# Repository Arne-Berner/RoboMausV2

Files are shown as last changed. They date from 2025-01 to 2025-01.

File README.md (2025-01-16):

# Goal
- build a micromouse (from here on out called "rat") from scratch

# Motivation
## The fear of the unknown
I have been working with electronics for a while now, but I never really got into PCB design. I always thought it was too complicated and I would never be able to do it. But I also always wanted to build a micromouse. So I thought, why not combine the two and learn something new in the process.

That being said I also wanted to use my 3D printer more and get rid of that fear that accompanies anything new. Doing this project I feel like I will be able to create electronic devices much more easily in the future. Not only because I learned some tricks on my way, but because I simply have done it before.

## Beginner to Intermediate Rust Project
Let's be honest, coding for embedded systems sound hard. Rust also sounds hard. But weirdly enough, those two things combined are much easier than I thought! I want to provide all the code I used for this project for anyone interested. If you feel like creating electronic devices could be fun, give it a try! Especially the esp32 and rust go really well together. You can [try out Rust on the ESP32 on Wokwi](https://wokwi.com/).

# Parts with their Voltage and Reason I used them

## Placed
### ESP32-s3-mini: 3.3V 
The reason I chose the s3-mini was because it wasn't much more expensive and I was not sure how much processing power will be needed for the project. If I had more time I probably would have chosen an esp32 from the c series. You don't need to use an esp32 at all for a micromouse, but I will need to send the map created by my SLAM-algorithm to my computer via wifi. The STM32 is the MCU that is used for most micromouse.

### USB-C: 5V output
Micro USB tend to break of more easily from PCBs and USB-C has the possibility of using more Volt in later designs, without changing too much.

### AMS1117-3.3: LDO that converts to 3.3V
This seems to be a very common LDO and even though the esp32 is somewhat capable of handling higher voltage than described in the datasheet, I didn't want my project to go up in flames at a bad time.

### L293D (better known as an H-Bridge)
This will let me use my 3.3V from the esp and my 8V from the LiPos to drive my motors. It usually takes one source that ranges from 5V to 36V and another source that will only take 5V. I will see how it works in the project. I could've used an smt h-bridge to minimize the size on the pcb, but running the h-bridge in the wrong manner can destroy it. If that happens (and it will happen) I would like to be able to replace it fast.

### TCS34725 (Color sensor): 2.7V - 3.6V / nom: 3V
I will need to detect the colors of certain places in the labyrinth as an extra task. This seems to be a common and cheap color sensor. It also has a rust library. 

### GY-521 or MPU-6050 (gyroscope sensor): 2.375V - 3.46V
This will help me position orientate my rat. I'm not sure yet, how I will combine this with the input I get from the encoder and what will be used primarily if there is a difference between the two. The mpu-6050 seems to be cheaper but has better specs.

## Not Placed
### SK6812MINI-B-012 (NeoPixel): 5V
This could be used for debugging purposes (and it looks cool), but it needs 5V and that would've drained the LiPos faster than I wanted them to. There is a 3V alternative to the 5V neopixel, but I could not find it on lcsc.

### AMS1117-5.0: LDO that converts to 5V
This would have been necessary if I used the Neopixel above or if the ams1117-3.3 would not be able to handle the lipo voltage.

# Learnings
## How to read a Datasheet instead of "read the datasheet"
When you start in electronics you hear "read the datasheet" a lot. It sounds like bad advice at first, because you probably are asking experienced people about very specific device and datasheets can be hundreds of pages long. Where to start reading up on it? What if there is a feature that you didn't know the name of? Most people rather stop than to "read the datasheet" without knowing where to look for the most important info. 

Later on it feels like "read the datasheet" really was the solution to most problems. But only seemingly so. Experts don't read the full datasheet, even if it is only a few pages long. They won't look at all the data. But they know how to skim the datasheet for the most important info and see if anything is readworthy. But I am no expert and I still need to find answers to my questions. So how to read a datasheet?

There are some basic informations that you most likely want to take a look at:
- volt and ampere (often found as VCC or Vin/Vout info)
- the pinout
- provided example schematics
- (footprints)
With those infos you will have most infos so that your ICs don't burst into flames. It also has the benefit, that most often when looking for those informations you will find other important or odd info that will help you with your project. Be aware that datasheets sometimes contain the data for many variations of IC.

## Copilot and co.
Reading the datasheet might be hard if it is in chinese or if it is hundreds of pages long. Using any LLM to get the gist of it or some pointers where to look for can be very helpfull. But be warned: Especially in electronics halucinations seem to occur very often. They should only be used, if you check the data afterwards. The pinout is very often wrong, the current and voltage vary from the real parts and you can't use it for example schematics. But it will give you words to look for in the datasheet that might be important. 

"What should I be aware of with part XY" or "What could go wrong with wiring X to Y" are the most helpfull prompts.

## Kicad
### Schematics
I like to start with everything at once and see everything come together at the end. But who would have thought that this is neither good in programming, nor in electronics? 

The next project I would definitely draw the schematics for only one or two parts and then check if everything is alright. Do some adjustments, check if everything is alright, put it in the pcb. Rinse and repeat. That way I wouldn't have had to redo big portions of the project and I would have been way faster. Not only that, but I would have some starting point when placing the footprints on the pcb.

Another trick I learned from a friend of mine named "MAG" is to take really good care of a global library and push it to github or any cloud provider. That way you can use it on any machine available to you and using github you could help other people by taking care of that library.

### Libraries and imports
Since I knew I wanted to get the pcb on jlcpcb I mainly used [this website](https://dougy83.github.io/jlcparts/#/) to find the right part. This is a fork of [this repository](https://github.com/yaqwsx/jlcparts) and should be part of that repository soon. It often makes sense to focus on one shop for electronic parts, since shipping and handling fees will stack up fast with different shops. I used [Easyeda cli Plugin](https://github.com/uPesy/easyeda2kicad.py) to get the libraries from EasyEda, since I figured they would fit the parts used by jlc the best.
If I were to start again I would probably use [this Import Plugin](https://github.com/Steffen-W/Import-LIB-KiCad-Plugin#use-of-the-application) instead or go the hard route and learn to draw my own footprints and symbols. Most people that have been doing this for a while seem to prefer using their own footprints. That way there will be no suprises when buying the pcb.

It's also worth mentioning, that adding test points to any power io seems like a good idea. Using test points in general for critical conditions can help tremendously. But what are critical areas? It depends on your project, but when something does not work, the first thing you check is probably the power supplies.

Lastly I have to admit that in most cases you do not need libraries or imports in a project, because kicads default library is very big. But the terms you might be looking for is not the term you are looking for. 

### Symbols
- Symbols are not the parts themselves, but a representation for them
- Symbols most often don't use the right pin attributes, but "unspecified", which results in a lot of errors when using easyeda2kicad
- GND and VCC are all "Power Input"
- Signals that could go in both ways are bidirectional
- Signals that go only in one way are input or output (which you won't find often and could make your life harder)
- a lot of warnings can be mitigated by using "passive" for pins, unless you know they are generating/receiving signals

### Footprints
- Footprints are the actual parts you would probably find. This abstraction between symbols and footprints confused me at first
- drawing them yourself can be a good practice, but the online libraries are much easier to use
- there is always a section about that on every datasheet
- most footprints are saved by their "package", so do not look for the specific ic in kicad, but for the packaging

### PCB
- One layer for horizontal signals and one layer for vertical signals
- Use more space first and then take away as much space as you need
- Draw a trace to see all the connected parts highlighted (this is good, when trying to find connected parts)
- there is a button to delete the whole trace (delete full track)
- there is a button to place a via on the current trace and change layer (place through via)
- put GND vias as close to the pad as possible and with a big trace to lower inductance
- you can use space to get some relative measurements. The origin of one of you coordinate systems in the bottom corner will change

### Planning and Assembly
Using an interactive BOM can be very usefull for any step, but especially the assembly can be structured that way. Checking if your parts are the way they should be, can be done with an interactive html. You can load it on your phone, you can export it for your other projects and you don't need to rewrite anything you don't need. I use the interactive BOM plugin for kicad.

For the actual assembly service on jlcpcb I use a plugin called "Fabrication Toolkit" which you can find in the plugin and content manager in kicad.

### Using Stencils
It can be usefull to place NPTH - holes that do not have any plating around them - to place the stencil properly. You can then use little pegs through both pcb and stencil to place the stencil very fast and accurately.

### Annoying things you want to know before they happen
- if you edit your symbols via schematics, they will only be updated for that one symbol in the schematics. There is no way to save that edit to your actual symbol in the library.
- if you have another window (e.g. the plugin window in the main menu) you cannot click anything in any other kicad window
- interactive bom gets cached, so you need to use ikognito mode
- interactive bom uses the generated bom fields for its fields. Those are only shown, if you updated the schematics editor and imported the changes into the pcb editor

Lastly I would advice you not to use the update pcb with relink too much, if you just used "annotate schematics". This will swap around parts and it's not fun.

## be a copycat
- you don't know what parts you need at the beginning. Just write "gyroscope pcb" on your prefered search or youtube to get a good idea, what might be usefull.

## PCB-Design
### 2 layer PCB vs 4 layer PCB
Truth being told, I have seen very different opinions on this. Some say 4 layers can get much more expensive. This is not necessarily the case when you only use through hole vias, but they are undeniably more expensive. But four layers are also a lot easier to design and depending on who you ask will make the signals less prone to EMI. 

As a rule of thumb I would say starting with a 2 layer pcb is the way to go and then go up to 4 layers, if you need to. For example when you have different voltages on your board that cannot easily be separate. But there is not much lost when you go for 4 layers from the beginning. Depending on how you click on what option in jlcpcb the price for this 4 layer board was 5$ more instead of the same size with 2 layers.

### Energie takes the path of least impedance, not resistance
Which makes a big difference in an AC Environment. But most hobby projects are DC, so why bother? Since any pulsed DC signal counts as a AC signal. This means for you, that you will have to keep the distance between the signal, ground and vcc very close to each other. This can be done via a good PCB layer stackup and thoughtfull routing.

### Signals will influence each other
Any Signal will be able to influence any other Signal next to it. Even though signals might look more tidies up, when you use the minimum distance possible by your PCB manufacturer, you should try to widen the gap between them. There is a tradeoff here, where some signals need to be coupled and some signals need to travel the shortest path possible.

### Important rules (that can be broken, if you know what you are doing) ... which I don't
- keep signals spaced as wide as possible
- short distance between forward and back pass
- keep GND and VCC via close to each other
- antennas work best with nothing in the way (place it at the edge)
- 3.3V signals should only reference 3.3V power in the current or next layer
- separate analog and digital signals spatially
- keep the distance between analog and digital 20x as wide as between ground and signal plane (no need to split the ground plane)
- different voltages get different areas on the board (the planes can be split if no other signals are crossing those areas)
- different frequencies get different areas on the board
- use ground vias to get signals from one layer to another
- don't put power and ground on layer 2 and 3 on a 4 layer board, because of the bigger distance
- on a 6 layer board don't put them on 2 and 5
- power layers should be near high-speed ICs
- use test pads
- PCB layers are stacked in pairs (distance wise)

# Resources
## Micromouse
There are some places to look at, but the best resource by far that I could find was [Micromouse Project from UCLA](https://projects.ieeebruins.com/micromouse/).

## PCB and KiCad
A video about proper grounding on pcb can be found [here](https://www.youtube.com/watch?v=ySuUZEjARPY&t=7540s&pp=ygURcGNiIGdyb3VuZCBwbGFuZSA%3D). [Robert Feranec](https://www.youtube.com/@RobertFeranec) also has very nice tutorials on different topics, even though they can be quite wordy. When it comes to nice and concise material I like [Phil's Lab](https://www.youtube.com/@PhilsLab). The audio is good, there are some good examples and he only concentrates on the most important points. Also the [getting started docs from KiCad](https://docs.kicad.org/8.0/en/getting_started_in_kicad/getting_started_in_kicad.html) are easy to read. Please let me know if you know any "non-youtube" sources that are well written!

## Rust
I have to admit, that after working through some nice [beginner std tutorials](https://docs.esp-rs.org/std-training/) (there is also [a no-std version](https://docs.esp-rs.org/no_std-training/)) which you can use with [Wokwi - an online esp32 simulator](https://wokwi.com/), I mostly look at the [esp-rs repos](https://github.com/esp-rs) and their respective examples. That is not the case because I am a hardcore "read the docs N00b" kinda person, but because the examples there and their docs are very well written and always up-to-date! 

But let's be serious, there always is a point, where you run into a wall with the docs, because you just don't know some technique that exists. The best place to find help then is [the esp matrix room](https://matrix.to/#/#esp-rs:matrix.org). There are a ton of helpfull people that will even answer the most basic questions in a respectful way. 

I think there should be an honorable mention for the [embedded rustaceans blog](https://blog.theembeddedrustacean.com/) which can help you at the beginning a lot and [awesome esp rust](https://github.com/esp-rs/awesome-esp-rust) which can be an inspiration for cool projects or topics you didn't know about.

# Next Versions
## learnings for V1
- [x] the holes for the case should be 3mm and those for the motors the small size
- [x] add pinheader for jtag
- [ ] add markings for + and - in the relevant places
- [x] gyroscope needs more space, to be able to be used in the middle
- [x] use jst-ph instead of xh
- [x] go up one size for smd. There is no benefit in 0403 when I solder it myself
- [x] use a stencil next time, when working with usb-c and Quad Flat No-Lead chips
- [ ] build cases for all the sensors/pcbs used
- [x] I don't need to care too much about interference from the motors for the usb since they will be turned off while flashing.
- [x] I want the testpoints near the peripheral they are for, because it's easier to test and see what is going on
- [ ] better naming and silkscreen helps a lot

## For Version 2
- [ ] make the LiPos chargeable
- [ ] use STM32 for the IR Sensors/ADC because they are less noisy
- [x] add proper silkscreen
I did think about adding lipo chargers, but:
1. It takes up some space to do that
2. It's hard to charge Lipos from one source in parallel
3. There are some nice TC4056 breakout boards which I can use, while running tests on the mouse

I did not use the STM32 for IR Sensors/ADC yet, because the quality of the IR sensor was somewhat sufficient and I needed to move fast, after Version 1 did not work at all.

## For Version 3
- [ ] connect ground to ground of the battery...
- [ ] use STM32 for the IR Sensors/ADC because they are less noisy
- [ ] get NPTH points for better alignment with the stencil
- [ ] go down to 2 layers so that it is cheaper to replicate

## What went wrong
I misunderstood "different voltages get different areas on the board (the planes can be split if no other signals are crossing those areas)". It means that you should split the power planes, if you have different voltages on your board. I thought it meant that you should split the ground planes beneath the power planes. There is no need for that, since in high frequency areas the signal will travel above the corresponding ground anyway. If it was closer to DC voltage, then it would just travel the shortes path through ground.

I definitely shouldn't have used a trackpad. My wrists hurt really bad and it was much slower than it needed to be.

I assumed that the adc multiplexing works across _all_ pins, but it only works for the first 14 or so. Testing every pin as I would like to use them on the board would have helped a lot!

## What went right
I could achieve a very small mouse with 4 layers. I'm not sure if I was able to do so with less layers.

I got over the fear of doing something for the first time and I learned a lot about electronics.

# Thanks
Hannes and Mohamad have helped me tremendously. Robert gave me some ideas for the next version and what I could have done better this time. Thank you!

# JLCPCB pricing
This has been really confusing to me, so that is why I am adding this section here. 
If you want to get your pcb from jlc pcb there are some weird things you have to look out for. For example, if you add a pcb with 4 layers from the beginning, it will have a lower price, than if you had added a 2 layer pcb and then changed it to a 4 layer pcb. The same goes for the size of the pcb. If you add a pcb with 100x100mm and then change it to 100x150mm it will be more expensive than if you had added a 100x150mm pcb from the beginning. 

Not only that, it gets really niche if you look at the assembly service. There are "basic", and "extended" parts. At least it looks like that. There are also "preferred extended" parts, which act like basic parts, if you use the "economic assembly". But first things first:
The assembly costs depending on what parts you choose. If you choose only basic parts and no special pcb, then this will get categorized as "economic assembly". That is the cheapest option you can get.

If you add "preferred extended" parts to this, it should stay in the "economic assembly" category. But if you add "extended" parts to this, it will get categorized as "standard assembly". This not only is the most expensive option, but you also have to pay 3$ for every _different_ extended part. So if you have some special transistor a thousand times on your board, that is 3$ extra for you. But if you have 10 different extended parts on your board, that is 30$ extra for you. This extra price comes from the fact, that they have to place those extended parts per hand into the machines, because they don't have the big reels for the most used parts.

Lastly there is a shipping option called "global direct standard line" which is much cheaper than the other options. 

## Some inaccurate information about the prices
- 2 layer 100x100mm: around 5$
- 4 layer 100x100mm: around 10$
- 4 layer bigger sizes: around 35 dollar$
- assembly economic: 7-10 dollar
- assembly standard: 20-30 dollar
- any extended part: 3 dollar
- global direct standard line: 2-5 dollar
- stencil: extra 2-20 dollar (mostly because of the shipping costs)

Overall I would say that small projects that don't need more than 2 layers should be done as such. Although 4 layers can give you a lot better signals and smaller boards, so I would always go for a 4 layer board that's smaller than 100x100 over a bigger 2 layer board.
The assembly is quite cheap, if you don't like soldering and would pay yourself for that time. The only problem is, that they don't have all the parts you might need and as soon as you use extended parts, it'll get really expensive really fast.

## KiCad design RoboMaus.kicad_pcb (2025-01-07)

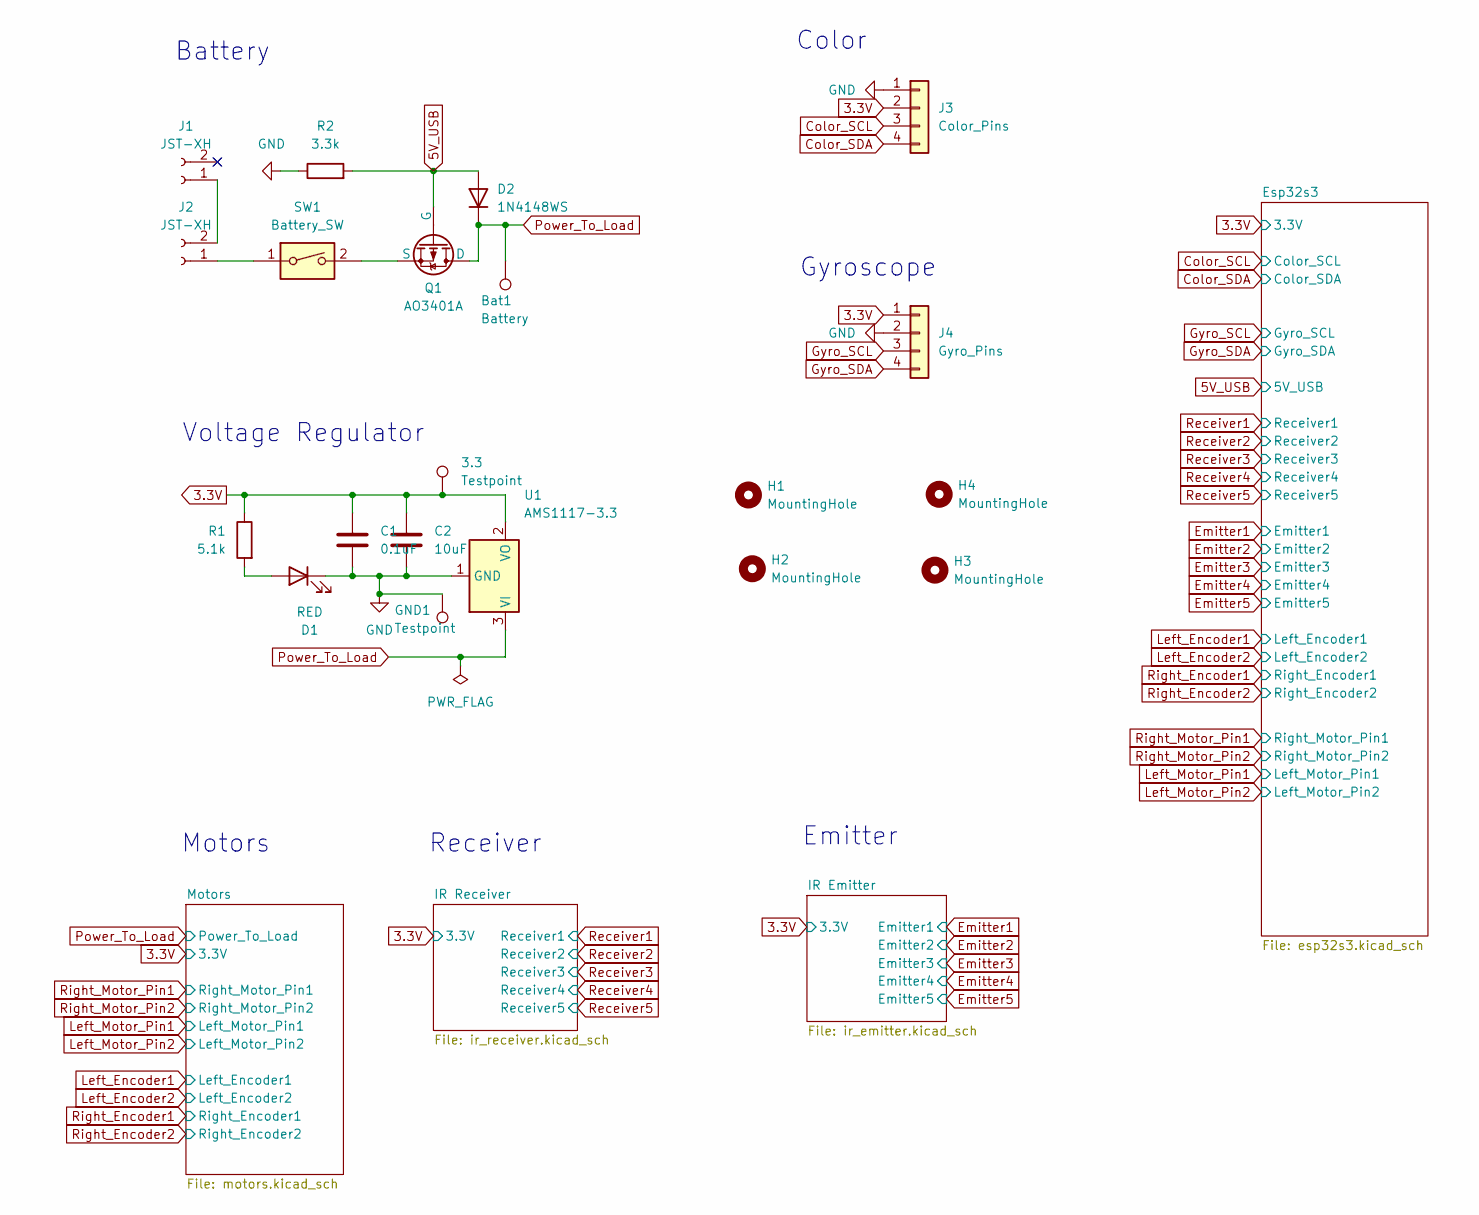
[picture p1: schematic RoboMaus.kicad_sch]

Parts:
3.3: Testpoint; TestPoint_THTPad_2.0x2.0mm_Drill1.0mm
Bat1: Battery; TestPoint_THTPad_2.0x2.0mm_Drill1.0mm
C1: 0.1uF; C_0805_2012Metric_Pad1.18x1.45mm_HandSolder
C2: 10uF; C_0805_2012Metric_Pad1.18x1.45mm_HandSolder
D1: RED; LED_0603_1608Metric_Pad1.05x0.95mm_HandSolder
D2: 1N4148WS; D_SOD-323; MPN 1N4148WS; JLCBasic basic
GND1: Testpoint; TestPoint_THTPad_2.0x2.0mm_Drill1.0mm
H1, H2, H3, H4: MountingHole; MountingHole_3.2mm_M3_DIN965_Pad
J1, J2: JST-XH; JST_XH_B2B-XH-A_1x02_P2.50mm_Vertical
J3: Color_Pins; PinHeader_1x04_P2.54mm_Vertical
J4: Gyro_Pins; PinHeader_1x04_P2.54mm_Vertical
Q1: AO3401A; SOT-23
R1: 5.1k; R_0603_1608Metric_Pad0.98x0.95mm_HandSolder; MPN 0603WAF5101T5E; JLCBasic basic
R2: 3.3k; R_0603_1608Metric_Pad0.98x0.95mm_HandSolder; MPN 0603WAF3301T5E; JLCBasic basic
SW1: Battery_SW; SW_DIP_SPSTx01_Slide_9.78x4.72mm_W7.62mm_P2.54mm
U1: AMS1117-3.3; SOT-223-3_TabPin2

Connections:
3.3V: 3.3.1, C1.1, C2.1, J3.2, J4.1, R1.1, U1.2 (VO); also elsewhere on the board
5V_USB: D2.2 (A), Q1.2 (G), R2.2; also elsewhere on the board
Color_SCL: J3.3; also elsewhere on the board
Color_SDA: J3.4; also elsewhere on the board
GND: C1.2, C2.2, D1.1 (K), GND1.1, J3.1, J4.2, R2.1, U1.1 (GND); also elsewhere on the board
Gyro_SCL: J4.3; also elsewhere on the board
Gyro_SDA: J4.4; also elsewhere on the board
unnamed: D1.2 (A), R1.2
unnamed: J1.1, J2.2
unnamed: J2.1, SW1.1
unnamed: Q1.3 (S), SW1.2
Power_To_Load: Bat1.1, D2.1 (K), Q1.1 (D), U1.3 (VI); also elsewhere on the board

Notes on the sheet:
Voltage Regulator
Battery
Emitter
Motors
Receiver
Gyroscope
Color

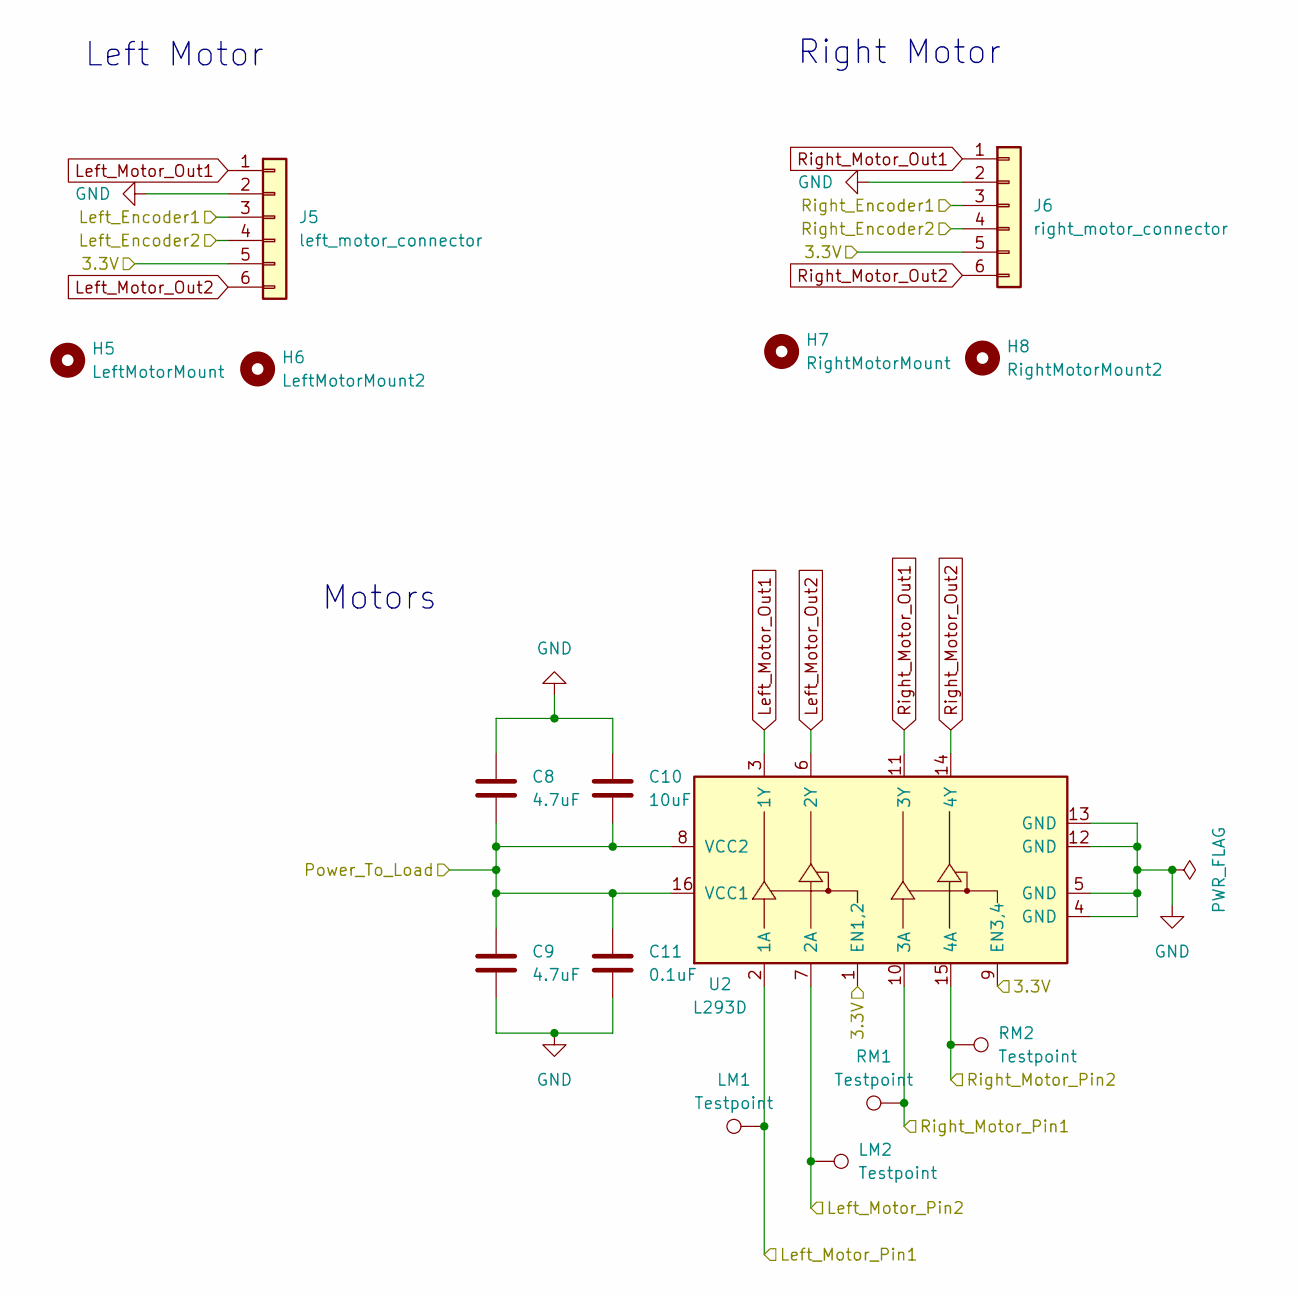
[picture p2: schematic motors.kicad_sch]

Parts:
C8, C9: 4.7uF; C_0805_2012Metric_Pad1.18x1.45mm_HandSolder
C10: 10uF; C_0805_2012Metric_Pad1.18x1.45mm_HandSolder
C11: 0.1uF; C_0805_2012Metric_Pad1.18x1.45mm_HandSolder
H5: LeftMotorMount; MountingHole_2.2mm_M2_DIN965_Pad
H6: LeftMotorMount2; MountingHole_2.2mm_M2_DIN965_Pad
H7: RightMotorMount; MountingHole_2.2mm_M2_DIN965_Pad
H8: RightMotorMount2; MountingHole_2.2mm_M2_DIN965_Pad
J5: left_motor_connector; JST_XH_B6B-XH-A_1x06_P2.50mm_Vertical
J6: right_motor_connector; JST_XH_B6B-XH-A_1x06_P2.50mm_Vertical
LM1, LM2: Testpoint; TestPoint_THTPad_2.0x2.0mm_Drill1.0mm
RM1, RM2: Testpoint; TestPoint_THTPad_2.0x2.0mm_Drill1.0mm
U2: L293D; DIP-16_W7.62mm

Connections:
3.3V: J5.5, J6.5, U2.1 (EN1,2), U2.9 (EN3,4); also elsewhere on the board
GND: C8.2, C9.2, C10.2, C11.2, J5.2, J6.2, U2.4 (GND), U2.5 (GND), U2.12 (GND), U2.13 (GND); also elsewhere on the board
Left_Encoder1: J5.3; also elsewhere on the board
Left_Encoder2: J5.4; also elsewhere on the board
Left_Motor_Out1: J5.1, U2.3 (1Y)
Left_Motor_Out2: J5.6, U2.6 (2Y)
Left_Motor_Pin1: LM1.1, U2.2 (1A); also elsewhere on the board
Left_Motor_Pin2: LM2.1, U2.7 (2A); also elsewhere on the board
Power_To_Load: C8.1, C9.1, C10.1, C11.1, U2.8 (VCC2), U2.16 (VCC1); also elsewhere on the board
Right_Encoder1: J6.3; also elsewhere on the board
Right_Encoder2: J6.4; also elsewhere on the board
Right_Motor_Out1: J6.1, U2.11 (3Y)
Right_Motor_Out2: J6.6, U2.14 (4Y)
Right_Motor_Pin1: RM1.1, U2.10 (3A); also elsewhere on the board
Right_Motor_Pin2: RM2.1, U2.15 (4A); also elsewhere on the board

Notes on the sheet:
Left Motor
Motors
Right Motor

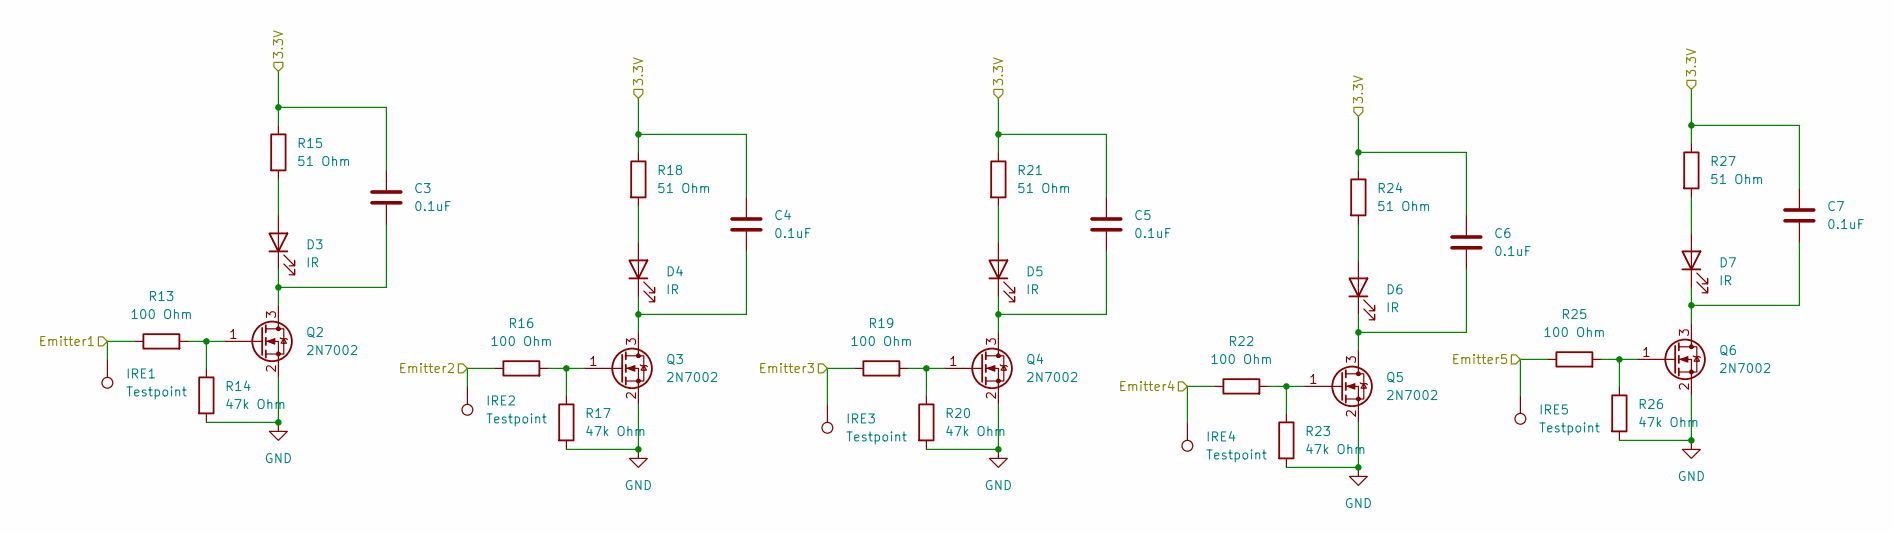
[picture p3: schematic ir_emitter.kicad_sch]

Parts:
C3, C4, C5, C6, C7: 0.1uF; C_0805_2012Metric_Pad1.18x1.45mm_HandSolder
D3, D4, D5, D6, D7: IR; LED_D5.0mm_IRGrey
IRE1, IRE2, IRE3, IRE4, IRE5: Testpoint; TestPoint_THTPad_2.0x2.0mm_Drill1.0mm
Q2, Q3, Q4, Q5, Q6: 2N7002; SOT-23
R13, R16, R19, R22, R25: 100 Ohm; R_0603_1608Metric_Pad0.98x0.95mm_HandSolder
R14, R17, R20, R23, R26: 47k Ohm; R_0603_1608Metric_Pad0.98x0.95mm_HandSolder
R15, R18, R21, R24, R27: 51 Ohm; R_0603_1608Metric_Pad0.98x0.95mm_HandSolder

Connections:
3.3V: C3.1, C4.1, C5.1, C6.1, C7.1, R15.1, R18.1, R21.1, R24.1, R27.1; also elsewhere on the board
Emitter1: IRE1.1, R13.1; also elsewhere on the board
Emitter2: IRE2.1, R16.1; also elsewhere on the board
Emitter3: IRE3.1, R19.1; also elsewhere on the board
Emitter4: IRE4.1, R22.1; also elsewhere on the board
Emitter5: IRE5.1, R25.1; also elsewhere on the board
GND: Q2.2 (S), Q3.2 (S), Q4.2 (S), Q5.2 (S), Q6.2 (S), R14.2, R17.2, R20.2, R23.2, R26.2; also elsewhere on the board
unnamed: D3.2 (A), R15.2
unnamed: C3.2, D3.1 (K), Q2.3 (D)
unnamed: D4.2 (A), R18.2
unnamed: C4.2, D4.1 (K), Q3.3 (D)
unnamed: D5.2 (A), R21.2
unnamed: C5.2, D5.1 (K), Q4.3 (D)
unnamed: D6.2 (A), R24.2
unnamed: C6.2, D6.1 (K), Q5.3 (D)
unnamed: D7.2 (A), R27.2
unnamed: C7.2, D7.1 (K), Q6.3 (D)
unnamed: Q2.1 (G), R13.2, R14.1
unnamed: Q3.1 (G), R16.2, R17.1
unnamed: Q4.1 (G), R19.2, R20.1
unnamed: Q5.1 (G), R22.2, R23.1
unnamed: Q6.1 (G), R25.2, R26.1

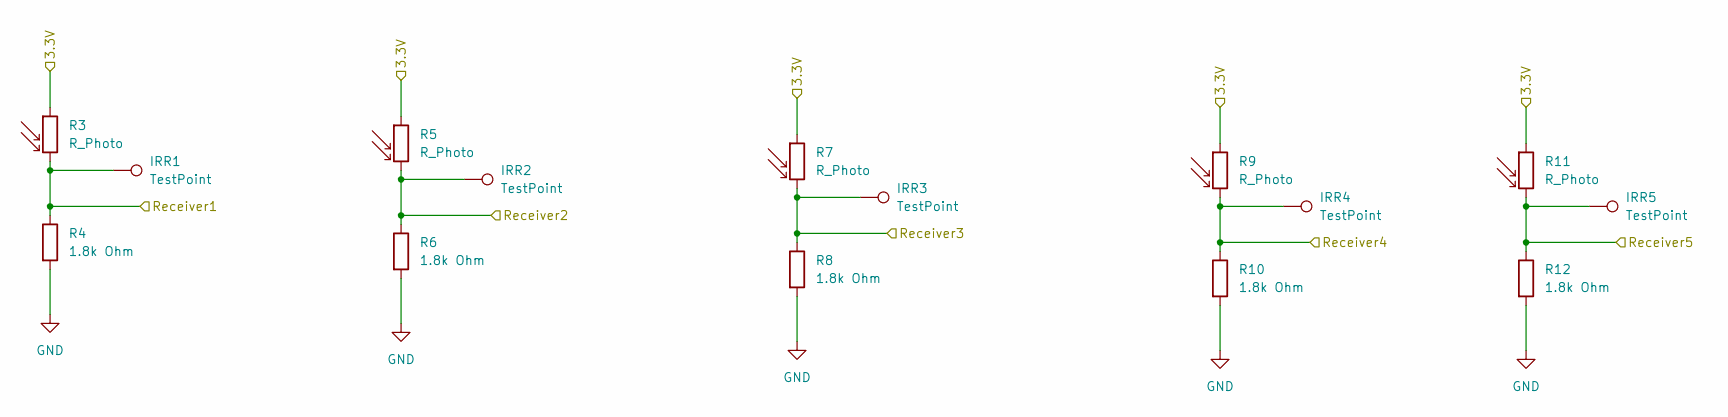
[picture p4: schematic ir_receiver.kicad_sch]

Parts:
IRR1, IRR2, IRR3, IRR4, IRR5: TestPoint; TestPoint_THTPad_2.0x2.0mm_Drill1.0mm
R3, R5, R7, R9, R11: R_Photo; LED_D5.0mm_IRBlack
R4, R6, R8, R10, R12: 1.8k Ohm; R_0603_1608Metric_Pad0.98x0.95mm_HandSolder

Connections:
3.3V: R3.1, R5.1, R7.1, R9.1, R11.1; also elsewhere on the board
GND: R4.2, R6.2, R8.2, R10.2, R12.2; also elsewhere on the board
Receiver1: IRR1.1, R3.2, R4.1; also elsewhere on the board
Receiver2: IRR2.1, R5.2, R6.1; also elsewhere on the board
Receiver3: IRR3.1, R7.2, R8.1; also elsewhere on the board
Receiver4: IRR4.1, R9.2, R10.1; also elsewhere on the board
Receiver5: IRR5.1, R11.2, R12.1; also elsewhere on the board

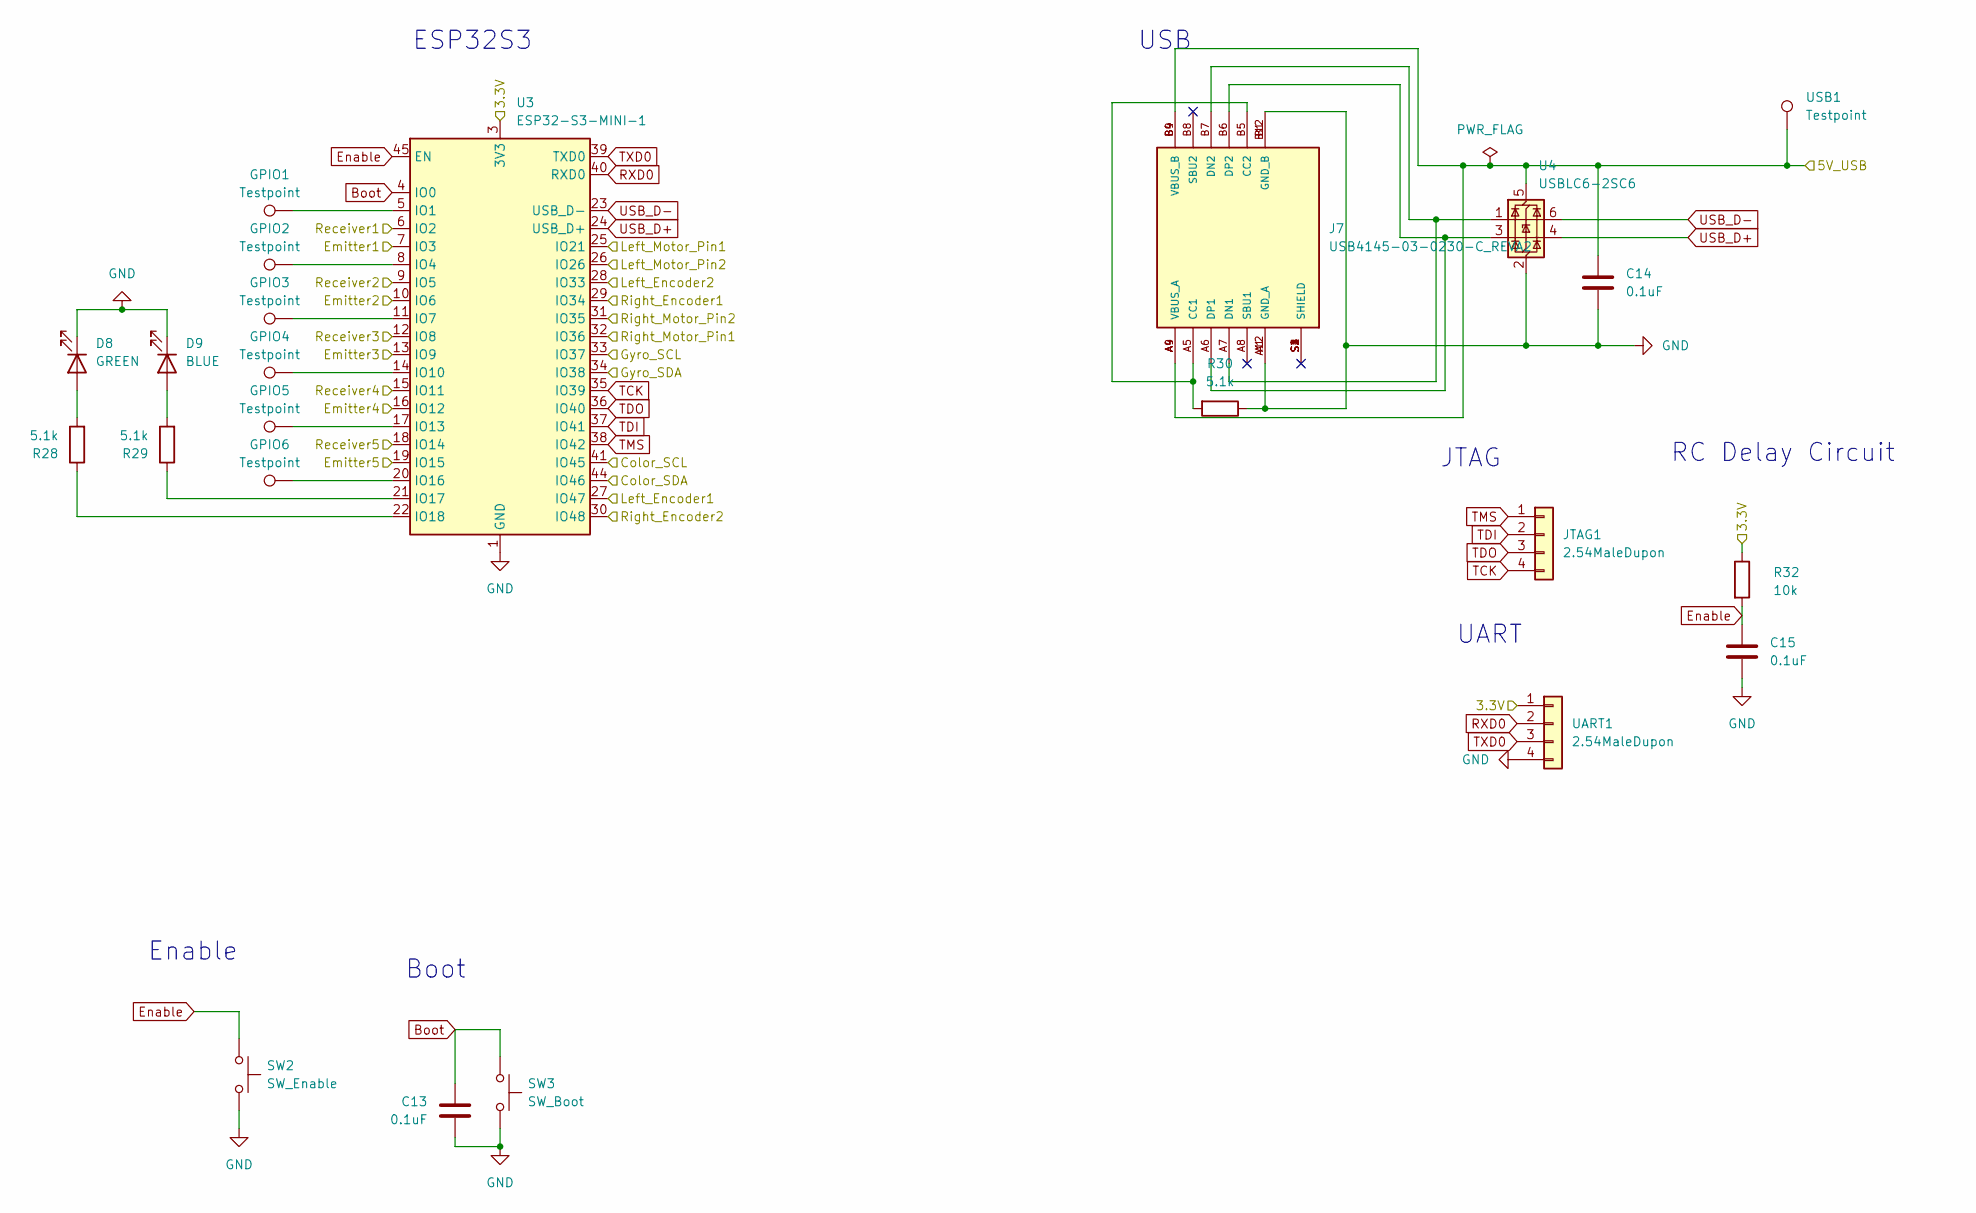
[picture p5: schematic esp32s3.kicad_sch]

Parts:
C13, C14, C15: 0.1uF; C_0805_2012Metric_Pad1.18x1.45mm_HandSolder
D8: GREEN; LED_0603_1608Metric_Pad1.05x0.95mm_HandSolder
D9: BLUE; LED_0603_1608Metric_Pad1.05x0.95mm_HandSolder
GPIO1, GPIO2, GPIO3, GPIO4, GPIO5, GPIO6: Testpoint; TestPoint_THTPad_2.0x2.0mm_Drill1.0mm
J7: USB4145-03-0230-C_REVA2; GCT_USB4145-03-0230-C_REVA2; PARTREV A2
JTAG1: 2.54MaleDupon; PinHeader_1x04_P2.54mm_Vertical
R28, R29, R30: 5.1k; R_0603_1608Metric_Pad0.98x0.95mm_HandSolder; MPN 0603WAF5101T5E; JLCBasic basic
R32: 10k; R_0603_1608Metric_Pad0.98x0.95mm_HandSolder; MPN 0603WAF3301T5E; JLCBasic basic
SW2: SW_Enable; SW_Push_1P1T_XKB_TS-1187A
SW3: SW_Boot; SW_Push_1P1T_XKB_TS-1187A
U3: ESP32-S3-MINI-1; ESP32-S2-MINI-1
U4: USBLC6-2SC6; SOT-23-6
UART1: 2.54MaleDupon; PinHeader_1x04_P2.54mm_Vertical
USB1: Testpoint; TestPoint_THTPad_2.0x2.0mm_Drill1.0mm

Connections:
3.3V: R32.1, U3.3 (3V3), UART1.1; also elsewhere on the board
5V_USB: C14.1, J7.A4 (VBUS_A), J7.A9 (VBUS_A), J7.B4 (VBUS_B), J7.B9 (VBUS_B), U4.5 (VBUS), USB1.1; also elsewhere on the board
Boot: C13.1, SW3.1, U3.4 (IO0)
Color_SCL: U3.41 (IO45); also elsewhere on the board
Color_SDA: U3.44 (IO46); also elsewhere on the board
Emitter1: U3.7 (IO3); also elsewhere on the board
Emitter2: U3.10 (IO6); also elsewhere on the board
Emitter3: U3.13 (IO9); also elsewhere on the board
Emitter4: U3.16 (IO12); also elsewhere on the board
Emitter5: U3.19 (IO15); also elsewhere on the board
Enable: C15.1, R32.2, SW2.1, U3.45 (EN)
GND: C13.2, C14.2, C15.2, D8.1 (K), D9.1 (K), J7.A1 (GND_A), J7.A12 (GND_A), J7.B1 (GND_B), J7.B12 (GND_B), R30.1, SW2.2, SW3.2, U3.1 (GND), U3.2 (GND), U3.42 (GND), U3.43 (GND), U3.46 (GND), U3.47 (GND), U3.48 (GND), U3.49 (GND), U3.50 (GND), U3.51 (GND), U3.52 (GND), U3.53 (GND), U3.54 (GND), U3.55 (GND), U3.56 (GND), U3.57 (GND), U3.58 (GND), U3.59 (GND), U3.60 (GND), U3.61 (GND), U3.62 (GND), U3.63 (GND), U3.64 (GND), U3.65 (GND), U4.2 (GND), UART1.4; also elsewhere on the board
Gyro_SCL: U3.33 (IO37); also elsewhere on the board
Gyro_SDA: U3.34 (IO38); also elsewhere on the board
Left_Encoder1: U3.27 (IO47); also elsewhere on the board
Left_Encoder2: U3.28 (IO33); also elsewhere on the board
Left_Motor_Pin1: U3.25 (IO21); also elsewhere on the board
Left_Motor_Pin2: U3.26 (IO26); also elsewhere on the board
unnamed: D8.2 (A), R28.2
unnamed: D9.2 (A), R29.2
unnamed: J7.A5 (CC1), J7.B5 (CC2), R30.2
unnamed: J7.A7 (DN1), J7.B7 (DN2), U4.1 (I/O1)
unnamed: J7.A6 (DP1), J7.B6 (DP2), U4.3 (I/O2)
unnamed: GPIO1.1, U3.5 (IO1)
unnamed: GPIO2.1, U3.8 (IO4)
unnamed: GPIO3.1, U3.11 (IO7)
unnamed: GPIO4.1, U3.14 (IO10)
unnamed: GPIO5.1, U3.17 (IO13)
unnamed: GPIO6.1, U3.20 (IO16)
unnamed: R29.1, U3.21 (IO17)
unnamed: R28.1, U3.22 (IO18)
RXD0: U3.40 (RXD0), UART1.2
Receiver1: U3.6 (IO2); also elsewhere on the board
Receiver2: U3.9 (IO5); also elsewhere on the board
Receiver3: U3.12 (IO8); also elsewhere on the board
Receiver4: U3.15 (IO11); also elsewhere on the board
Receiver5: U3.18 (IO14); also elsewhere on the board
Right_Encoder1: U3.29 (IO34); also elsewhere on the board
Right_Encoder2: U3.30 (IO48); also elsewhere on the board
Right_Motor_Pin1: U3.32 (IO36); also elsewhere on the board
Right_Motor_Pin2: U3.31 (IO35); also elsewhere on the board
TCK: JTAG1.4, U3.35 (IO39)
TDI: JTAG1.2, U3.37 (IO41)
TDO: JTAG1.3, U3.36 (IO40)
TMS: JTAG1.1, U3.38 (IO42)
TXD0: U3.39 (TXD0), UART1.3
USB_D+: U3.24 (USB_D+), U4.4 (I/O2)
USB_D-: U3.23 (USB_D-), U4.6 (I/O1)

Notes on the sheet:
JTAG
Boot
USB
ESP32S3
RC Delay Circuit
UART
Enable

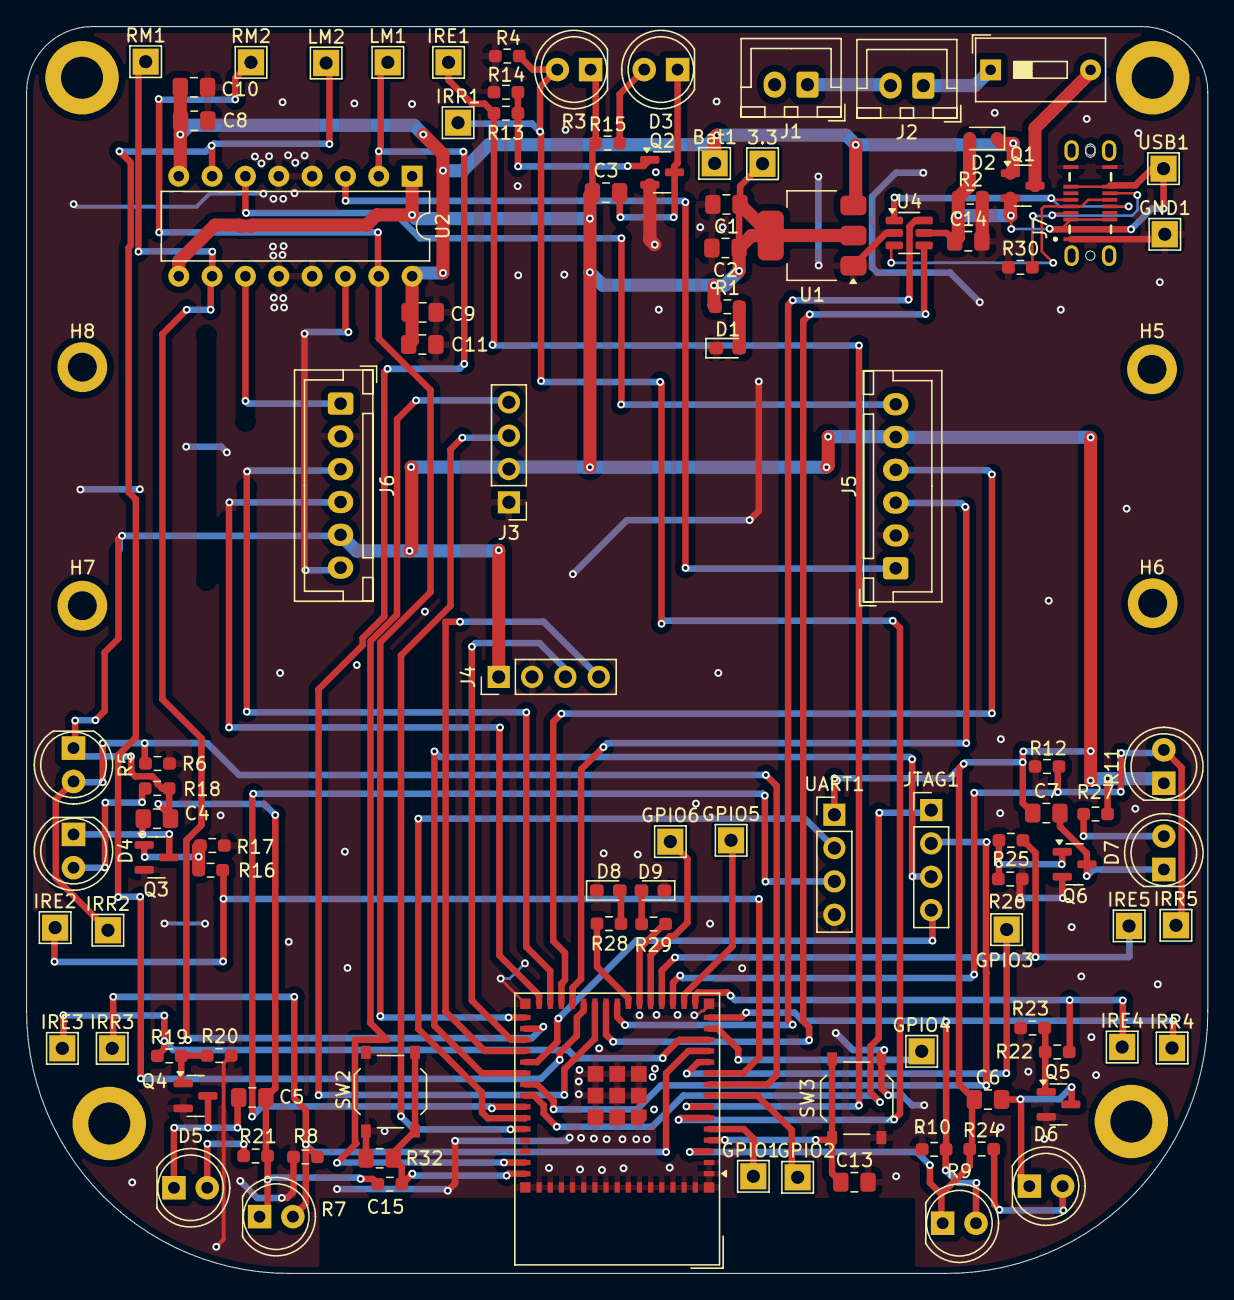
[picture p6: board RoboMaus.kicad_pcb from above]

Board: 4 copper layers, 90.0 x 95.0 mm, 108 parts (0 on the bottom side), 72 nets.

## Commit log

2025-01-03 feat:initial commit
    [RoboMaus.kicad_pcb, RoboMaus.kicad_sch, esp32s3.kicad_sch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]
2025-01-03 schematic: all errors and warnings gone
    [RoboMaus.kicad_pcb, RoboMaus.kicad_sch, esp32s3.kicad_sch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]
2025-01-04 pcb: all wired up, most warnings can't be fixed.
    [RoboMaus.kicad_pcb, RoboMaus.kicad_sch, esp32s3.kicad_sch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]
2025-01-04 pcb: fixed the wrong mounting holes...
    [RoboMaus.kicad_pcb]
2025-01-07 docs: some notes about getting the stencil right
    [RoboMaus.kicad_pcb]
2025-01-07 docs: kicad uses packaging not ics
2025-01-07 docs: kicad uses packaging not ics.. the right way
2025-01-16 docs: I forgot to connect the battery ground
